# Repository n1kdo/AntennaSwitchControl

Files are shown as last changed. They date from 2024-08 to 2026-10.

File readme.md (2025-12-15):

# N1KDO IOT Antenna Switch Control

This project is intended to operate a remote antenna switch.  

It supports (up to) a 2-radio, 8-antenna switch.  2x6 switches for fine.  Active-hi
or active low compatible.

Why IOT?  That's really about WiFi.  The board uses WiFi to connect to your network,
which means that only the power leads need to be protected from Zeus, not 14 +/- wires.  

I have built matching "band-decoders" to interface with my Elecraft HF radios.  
The band decoders detect a band change on the radio and send a API request to 
the switch control board to request an antenna for that band.  If no antenna 
is available, the band decoder will activate the K3s' "TX INHIBIT" lead and 
prevent the radio from transmitting into the wrong antenna or no antenna.

The Band Selector (radio interface) is [here](https://github.com/n1kdo/BandSelector) &mdash;
This is the other component for this project, you will need _two_ &mdash;  one for each radio.

See the Ecosystem diagram, below.

## Ecosystem

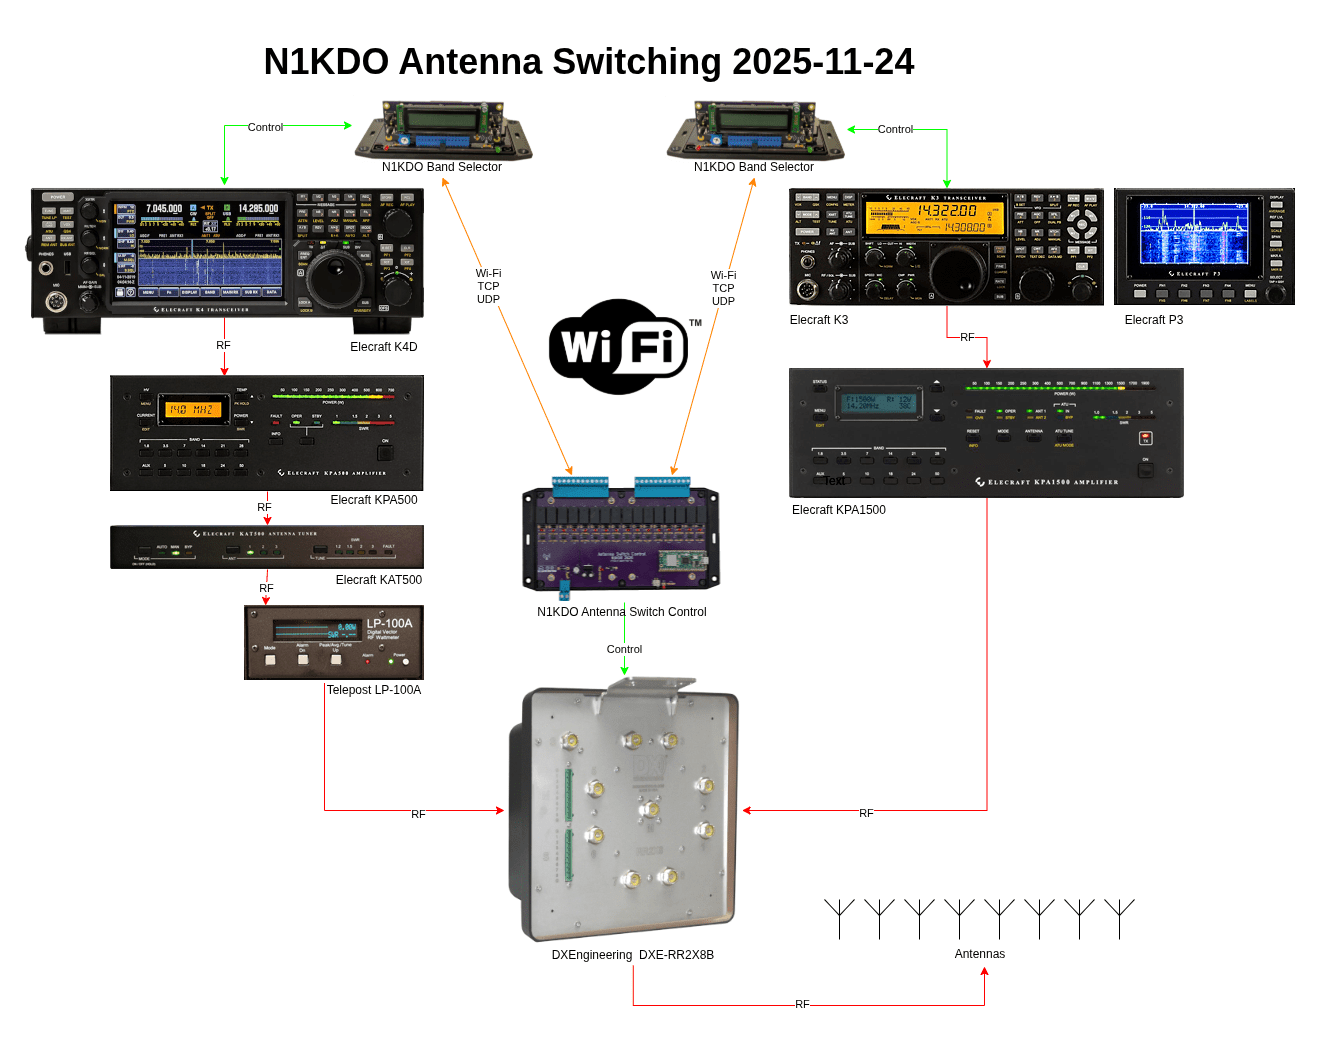
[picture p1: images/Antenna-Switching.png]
Ecosystem


## Bill of Materials

* [Bill of Materials](BOM.md)
* The approximate cost to buy these parts is about $106.

## Board Image

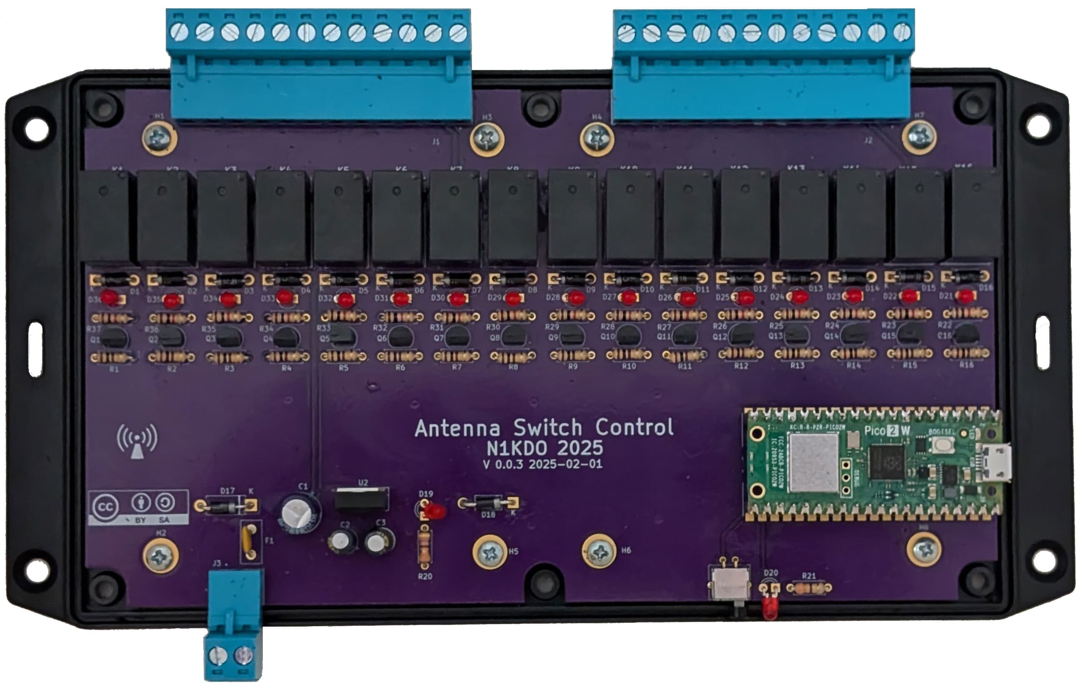
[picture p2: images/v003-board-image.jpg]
Board Image


# UI Images

## "Control Panel" Image

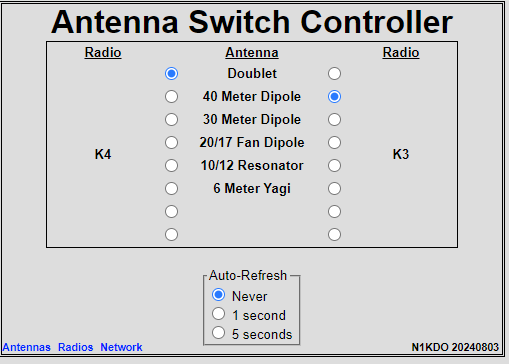
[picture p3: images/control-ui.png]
Control UI


## Antenna Setup UI

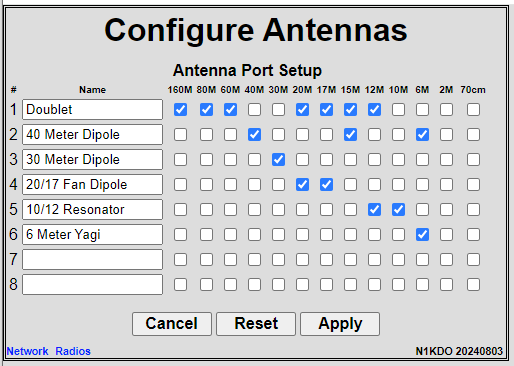
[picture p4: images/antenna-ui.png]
Antenna Setup UI


## Radio Setup UI

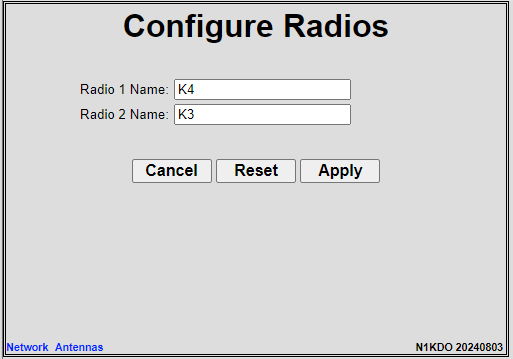
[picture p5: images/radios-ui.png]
Radio Setup UI


## Network Setup UI

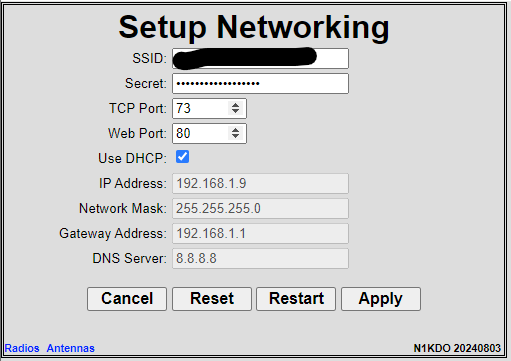
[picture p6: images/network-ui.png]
Network Setup UI


n1kdo 20251124

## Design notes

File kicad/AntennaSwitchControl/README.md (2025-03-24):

# Antenna Switch Control (Hardware)

This is a board that allows a Raspberry Pi Pico-W to control 16 SPST relays.

The original purpose is to provide better automation for a 2-in, 6-out remote antenna switch, but
it is built with extra capacity to allow a 2-in, 8-out remote switch as well.

## 3D image from KiCad
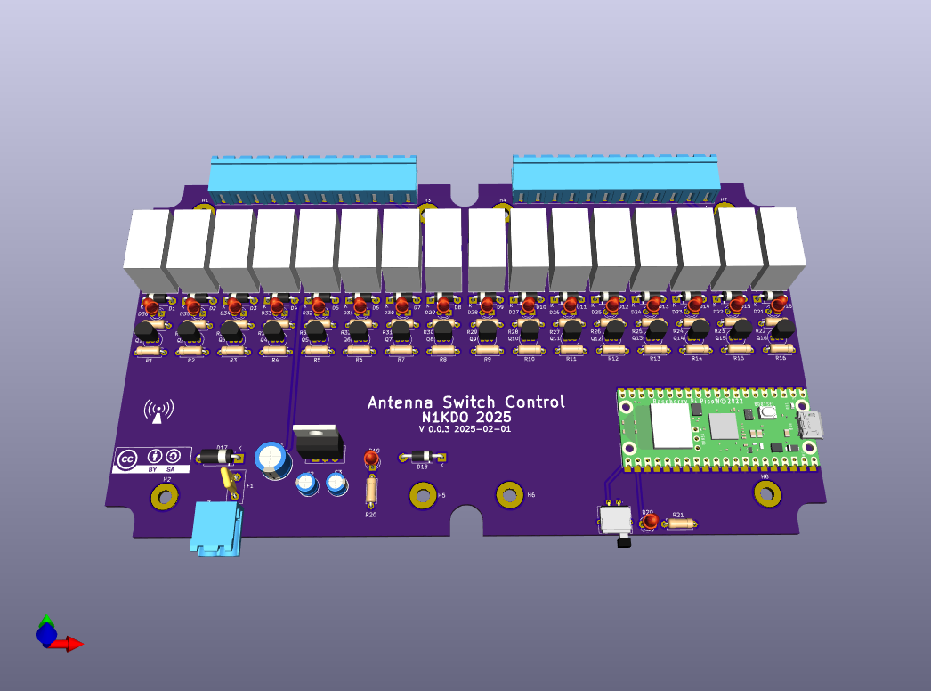
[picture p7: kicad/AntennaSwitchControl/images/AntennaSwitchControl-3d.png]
3d image


## Real World Image

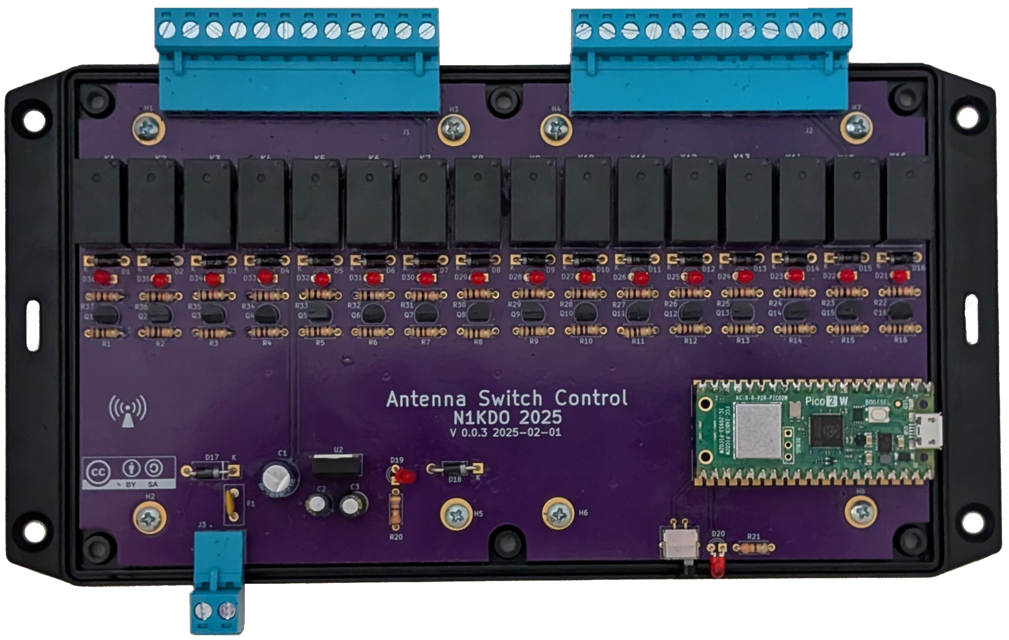
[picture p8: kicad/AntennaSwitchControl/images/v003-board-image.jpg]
Real-World Image


20250324 n1kdo

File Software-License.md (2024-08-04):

# BSD 2-Clause License

**Copyright (c) 2024, Jeffrey B. Otterson, N1KDO**

All rights reserved.

Redistribution and use in source and binary forms, with or without
modification, are permitted provided that the following conditions are met:

* Redistributions of source code must retain the above copyright notice, this
  list of conditions and the following disclaimer.

* Redistributions in binary form must reproduce the above copyright notice,
  this list of conditions and the following disclaimer in the documentation
  and/or other materials provided with the distribution.

**THIS SOFTWARE IS PROVIDED BY THE COPYRIGHT HOLDERS AND CONTRIBUTORS "AS IS"
AND ANY EXPRESS OR IMPLIED WARRANTIES, INCLUDING, BUT NOT LIMITED TO, THE
IMPLIED WARRANTIES OF MERCHANTABILITY AND FITNESS FOR A PARTICULAR PURPOSE ARE
DISCLAIMED. IN NO EVENT SHALL THE COPYRIGHT HOLDER OR CONTRIBUTORS BE LIABLE
FOR ANY DIRECT, INDIRECT, INCIDENTAL, SPECIAL, EXEMPLARY, OR CONSEQUENTIAL
DAMAGES (INCLUDING, BUT NOT LIMITED TO, PROCUREMENT OF SUBSTITUTE GOODS OR
SERVICES; LOSS OF USE, DATA, OR PROFITS; OR BUSINESS INTERRUPTION) HOWEVER
CAUSED AND ON ANY THEORY OF LIABILITY, WHETHER IN CONTRACT, STRICT LIABILITY,
OR TORT (INCLUDING NEGLIGENCE OR OTHERWISE) ARISING IN ANY WAY OUT OF THE USE
OF THIS SOFTWARE, EVEN IF ADVISED OF THE POSSIBILITY OF SUCH DAMAGE.**

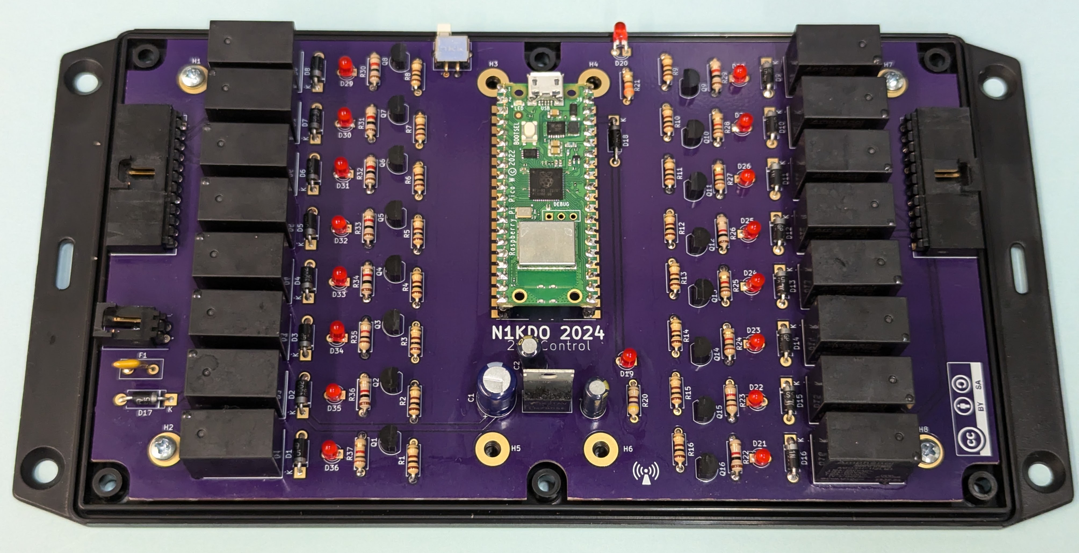
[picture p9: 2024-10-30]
kicad/AntennaSwitchControl/images/16-relays-reality.jpg

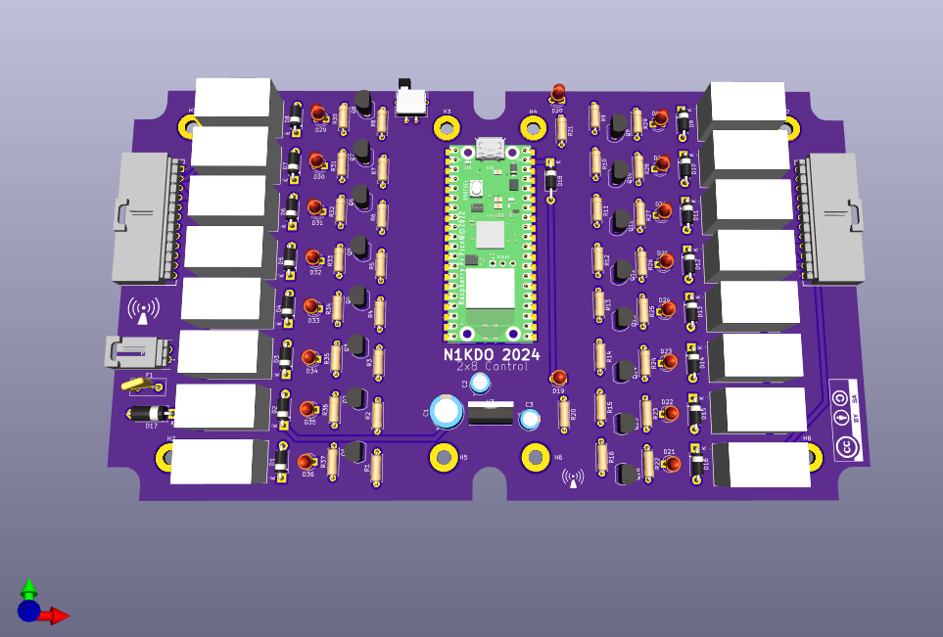
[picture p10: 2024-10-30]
kicad/AntennaSwitchControl/images/3d-render.png

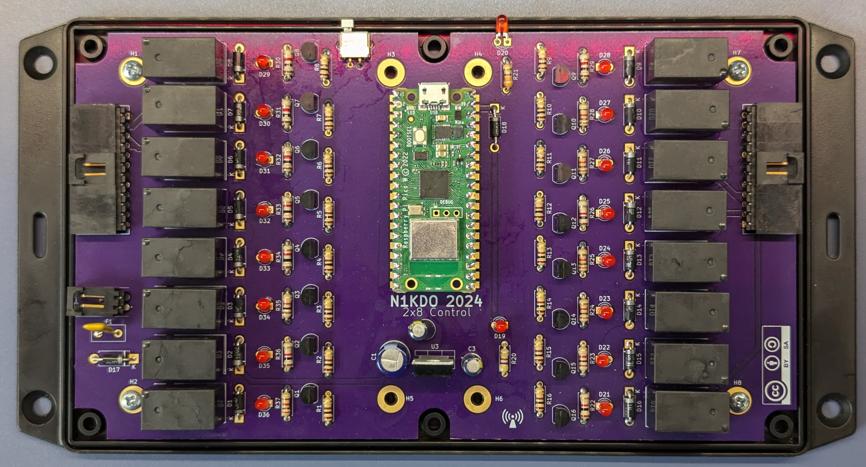
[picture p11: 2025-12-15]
images/board-image.jpg

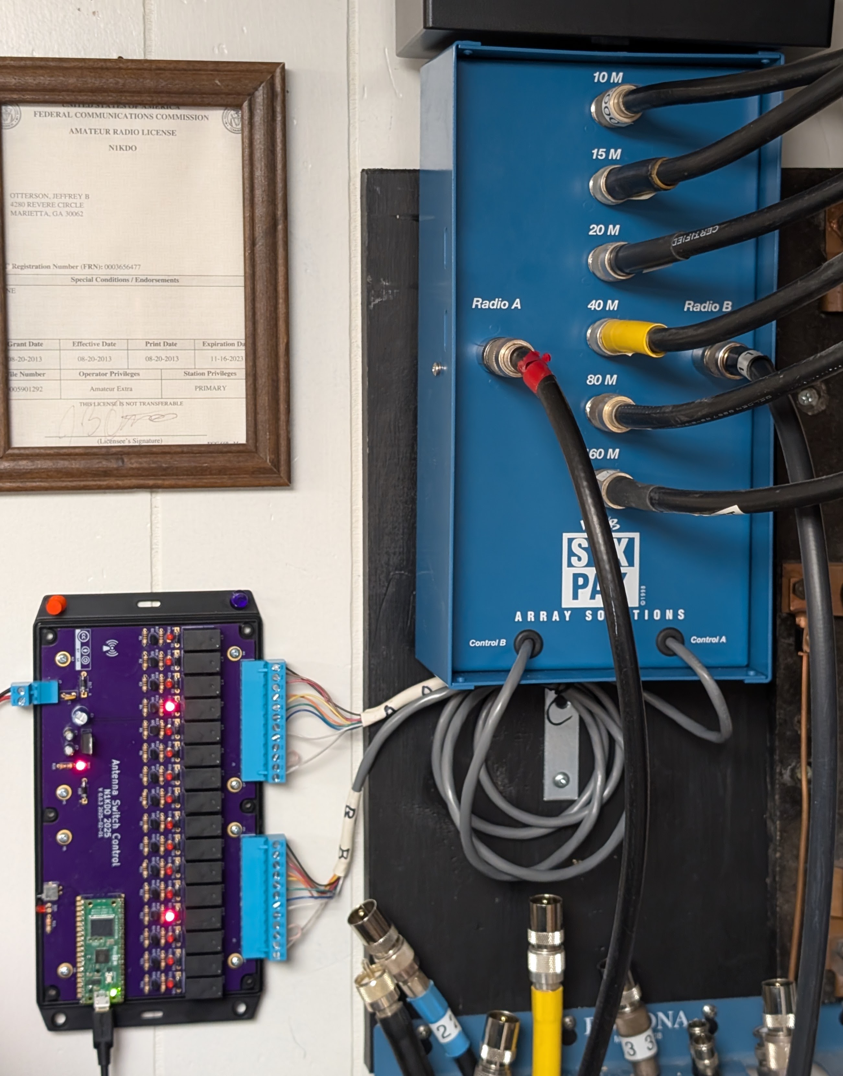
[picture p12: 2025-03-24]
images/with-six-pak.jpg

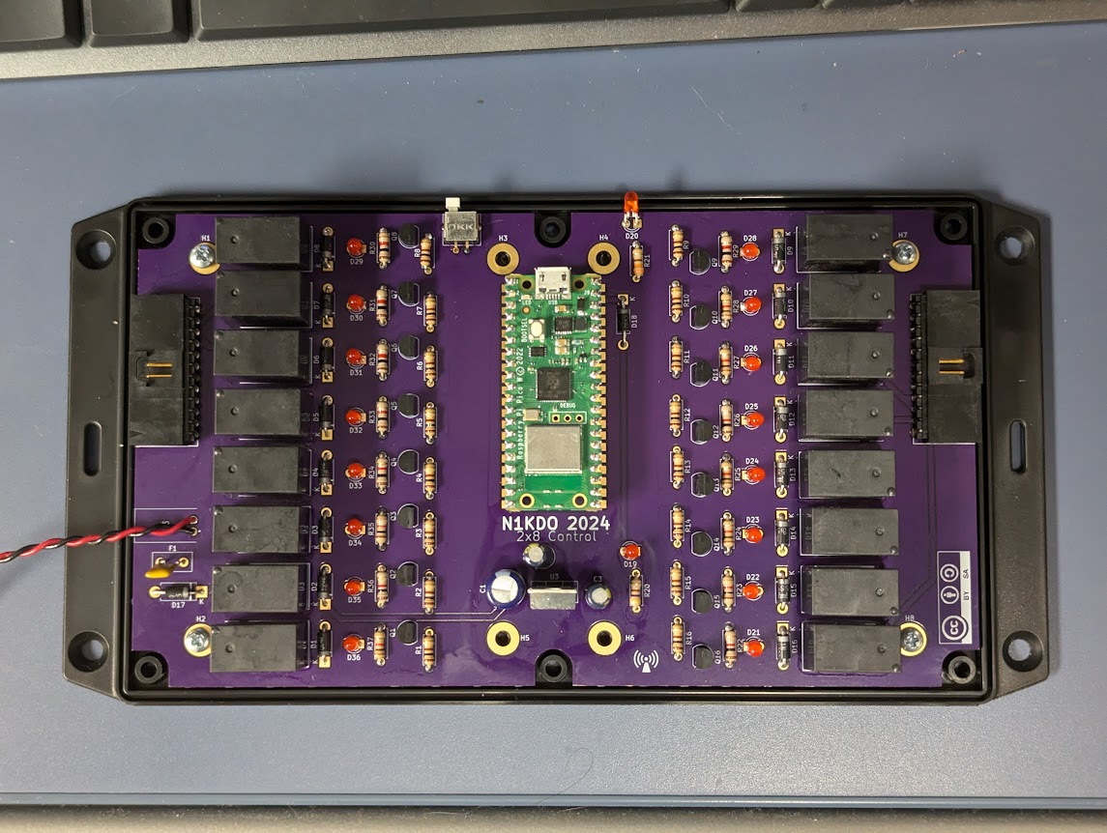
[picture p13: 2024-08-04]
images/board-image.png

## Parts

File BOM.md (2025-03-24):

# Bill of Materials for Antenna Switch Controller

This is the Bill of Materials for the N1KDO Antenna Switch Controller.

All the parts -- except the circuit boards -- were ordered from Mouser.com.

The circuit boards came from Oshpark.com.

## Antenna Switch Controller Board Bill of Materials

| ID | Description | Manufacturer | Part Number | Qty | Price | Extended |
|---|---|---|---|----:|---:|---:|
| C1 | Aluminum Electrolytic Capacitors - Radial Leaded 220uF 25V | Panasonic | ECA-1EM221 | 1 |  0.28 | 0.28 |
| C2,C3 | Aluminum Electrolytic Capacitors - Radial Leaded 2.2uF 50volts AEC-Q200 | Panasonic | EEU-FC1H2R2H | 2 |  0.12 | 0.24 |
| D1,D2,D3,D4,D5,D6,D7,D8,D9,D10,<br/>D11,D12,D13,D14,D15,D16,D17 | Rectifiers Diode - DO-41 - 100V - 1A | Diotec | 1N4002 |  17 |  0.06 | 1.02 |
| D18 | Schottky Diodes & Rectifiers Vr/40V Io/1A | STMicroelectronics | 1N5819 | 1 |  0.21 | 0.21 |
| D19,D20,D21,D22,D23,D24,D25,D26,D27,<br/>D28,D29,D30,D31,D32,D33,D34,D35,D36 | Standard LEDs - Through Hole Red Diffused | Lite-On | LTL-4221N |  18 |  0.19 | 3.42 |
| F1 | Resettable Fuses - PPTC .9A 30V 100A Imax | LittelFuse | RUEF090 | 1 |  0.61 | 0.61 |
| J1,J2 | Pluggable Terminal Blocks 2 24 Poles, Pluggable, Receptacle, Horizontal, 5.0 Pitch, Terminal Block  | SameSky | TBP04R1-500-12BE | 2 |  1.12 | 2.24 | 
| J3 | Pluggable Terminal Blocks 2 24 Poles, Pluggable, Receptacle, Horizontal, 5.0 Pitch, Terminal Block  | SameSky | TBP04R1-500-02BE | 1 |  0.43 | 0.43 |
| K1,K2,K3,K4,K5,K6,K7,K8,<br/>K9,K10,K11,K12,K13,K14,K15,K16 | General Purpose Relays Commercial Relay Rated Carrying Current 10A | Amphenol Anytek | AHQSH112LM100G |  16 |  0.53 | 8.48 |
| Q1,Q2,Q3,Q4,Q5,Q6,Q7,Q8,<br/>Q9,Q10,Q11,Q12,Q13,Q14,Q15,Q16 | MOSFET 60V 200mA 5 Ohm Single N-Channel TO-92 | onsemi / Fairchild | 2N7000 |  16 |  0.38 | 6.08 |
| R1,R2,R3,R4,R5,R6,R7,R8<br/>R9,R10,R11,R12,R13,R14,R15,R16 | Carbon Film Resistors - Through Hole 1/4W 100 Ohm 5% | Yageo | CFR-25JB-52-100R |  15 |  0.04 | 0.60 |
| R20 | Carbon Film Resistors - Through Hole 1/4W 470 Ohm 5% | Yageo | CFR-25JB-52-470R | 1 |  0.02 | 0.02 |
| R21 | Carbon Film Resistors - Through Hole 1/4W 330 Ohm 5% | Yageo | CFR-25JB-52-330R | 1 |  0.02 | 0.02 |
| R22,R23,R24,R25,R26,R27,R28,R29,<br/>R30,R31,R32,R33,R34,R35,R36,R37 | Carbon Film Resistors - Through Hole 1 kOhms 250 mW 5 % | Yageo | CFR-25JB-1K0 |  16 |  0.02 | 0.32 |
| SW1 | Pushbutton Switches SPST OFF(ON) R/A WHT | NKK Switches | GB215AH-B | 1 |  4.35 | 4.35 |
| SW1 (cap) | Switch Bezels / Switch Caps .157" RND BLK CAP | NKK Switches | AT4063A | 1 |  0.52 | 0.52 |
| U1 | Single Board Computers Raspberry Pi Pico 2 W | Raspberry Pi | SC1633 | 1 |  7.00 | 7.00 |
| U3 | Linear Voltage Regulators 5.0V 1.5A Positive | STMicroelectronics | L7805CV | 1 |  0.48 | 0.48 |
| Enclosure | Enclosures, Boxes, & Cases FR ABS w/Flanged Lid 7.6x4.4x2.2" Black | Hammond Manufacturing | 1591XXEFLBK | 1 | 12.84 | 12.84 |
| P1, P2 | Pluggable Terminal Blocks 2 24 Poles, Pluggable, Horizontal, 5.0 Pitch, 28 12 (AWG), Terminal Block | SameSky | TBP04P1-500-12BE | 2 |  2.52 | 5.04 |
| P3 | Pluggable Terminal Blocks 2 24 Poles, Pluggable, Horizontal, 5.0 Pitch, 28 12 (AWG), Terminal Block | SameSky | TBP04R1-500-02BE | 1 |  0.83 | 0.83 |
| PCB | N1KDO Antenna Switch Control PCB Band Selector Board PCB V 0.0.3 | Oshpark | | 1 | 50.08 | 50.08 |
| **Total** | | | | | | **105.11** |

Approximate Total Project Cost $106.

n1kdo 20250324

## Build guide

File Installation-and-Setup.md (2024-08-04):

# Installation and Setup

This page describes how to install and set up this project.

There are three main steps:

1. Installing Micropython
2. Installing the Python code.
3. Connecting to your Wi-Fi network.

## Installing MicroPython on your Pico-W

1. Download the latest stable build of [Pico W MicroPython](https://micropython.org/download/RPI_PICO_W/). 
   [This is the direct link](https://micropython.org/resources/firmware/RPI_PICO_W-20240105-v1.22.1.uf2).
2. Connect a micro-USB cable to your PC.  Hold down the white "BOOTSEL" button on the Pico-W, and insert the
   micro-USB cable into your Pico-W.
3. The Pico-W should appear as a USB storage device on your computer.  On mine, it shows up as "RPI-RP2 (F:)".
4. Copy/Paste the MicroPython .uf2 file to this drive.
5. Disconnect the Pico-W and prepare for the next step.

## Installing this software onto the Pico-W

The easiest way to get this software installed onto your Pico-W is to use the `loader.py` tool, also
provided in this repository.  

Note that these commands are written from a Windows perspective, but the Python commands should work the same way 
on macOS or Linux.  I have no Macs, so I cannot test this.

1. Download Python 3 from https://www.python.org/downloads/ and install it.  Make sure to select "Add 
   Python 3 to Path."
2. Download the contents of this GitHub repository as a zip.  Use
   [this URL](https://github.com/n1kdo/switch-control/archive/refs/heads/master.zip)
3. Unpack that zip file somewhere. 
4. Open a command prompt.  (your choice.  Could be PowerShell, could be good old CMD.)
5. From the command line, execute the following command: `pip install pyserial` -- this will install the Python 
   serial port support.
6. Change directory to where you unpacked the GitHub zip file, and then change directory to the `src/loader` directory.
7. From the command line, execute the following command: `python loader.py` -- this will install all the python  
   software onto the Pico-W.

If you want to experiment, you can use the open-source "Thonny" IDE to load the python source code and HTML files
onto the Pico W.  Unfortunately, Thonny cannot load binary files, but you can work around this "upload" feature in
the "Files" page.

## Setup and Connecting to your Wi-Fi Network

The software has a setup web page that allows you to set the SSID and secret to connect to you Wi-Fi network, 
but how can you access this page if the controller is not already connected to your network? This is the function
of the "mode" button. When the mode button is pressed, the device will restart as a Wi-Fi access point named
"kpa500" using password "elecraft".  Connect to this access point with your phone or other Wi-Fi device. Some 
devices will complain that this network does not offer Internet access--that is ok, because it does not! 
You may need to check a box to keep your device connected to this network.

Once connected to the "kpa500" network, open the device's web page by accessing http://192.168.4.1 – from here you
can click the "Setup" link and configure the network. After you enter your network’s SSID and secret, click the "Apply"
button to save the configuration, and then press the "Restart" button to return the device to normal mode.

Access point mode can also be used in locations where there is no Wi-Fi service, the device is completely 
usable in access point mode.

## Electrical Connections

(To be added.  Meanwhile, consult the schematic.)

## Controls and Indicators

| Control/Indicator | Purpose |
|---|---|
| LED D20 | Status indicator |
| Switch SW1 | Mode Selector |

The Status Indicator normally blinks out the device's IP address in slow Morse code.  
When the device is configured in Access Point mode, it will blink out "AP" followed by the device's IP address. 
If the device cannot connect to the Wi-Fi network, it will blink "ERR" in Morse code.

Hold down the Mode Selector button two seconds to switch the device in or out of Access Point Mode (for configuring
the Wi-Fi network.) The device will restart, and you should see a different message blinking out in Morse code.

## What is all this software stuff, anyway?

Here's a brief guide to what all code is...

### Application files:

This table describes what the source modules do.

| Filename | Description |
|---|---|
| src/switch-control/http_server.py | this is a lightweight HTTP ("web") server. |
| src/switch-control/main.py | mainline program. |
| src/switch-control/micro_logging.py | lightweight logging, similar to Python's 'logging' |
| src/switch-control/morse_code.py | code to send morse code on the LED.  Not all letters are included to save space. |
| src/switch-control/not_machine.py | mock 'machine' interface, for debugging on platforms other than MicroPython. |
| src/switch-control/picow_network.py | networking common code for Pico-W |
| src/switch-control/relays.py | relay control code |
| src/switch-control/utils.py | common utility functions |
| src/switch-control/content/antennas.html | Antennas Configuration page |
| src/switch-control/content/favicon.ico | Icon for web site |
| src/switch-control/content/files.html | Files page |
| src/switch-control/content/network.html  | Network Configuration Page |
| src/switch-control/content/radios.html | Radios Configuration Page |
| src/switch-control/content/switch.html | Switch Control Panel Page |
| src/switch-control/data/config.json | configuration file for device. |

Note that it is possible to modify any of the User Interface pages.  The software wants to protect these files, you
will need to upload them using a different name, and then rename them.

If you feel adventurous, you can modify the `config.json` file to set your Wi-Fi SSID and secret prior to loading the
software.

### Additional Stuff

Here's the code that makes up the "Easy Loader".

| Filename | Description |
|---|---|
| src/loader/loader.py  | tool to more easily install Python code on Pico W |
| src/loader/pyboard.py | code to allow communication and control of MicroPython boards, used by loader.py. |

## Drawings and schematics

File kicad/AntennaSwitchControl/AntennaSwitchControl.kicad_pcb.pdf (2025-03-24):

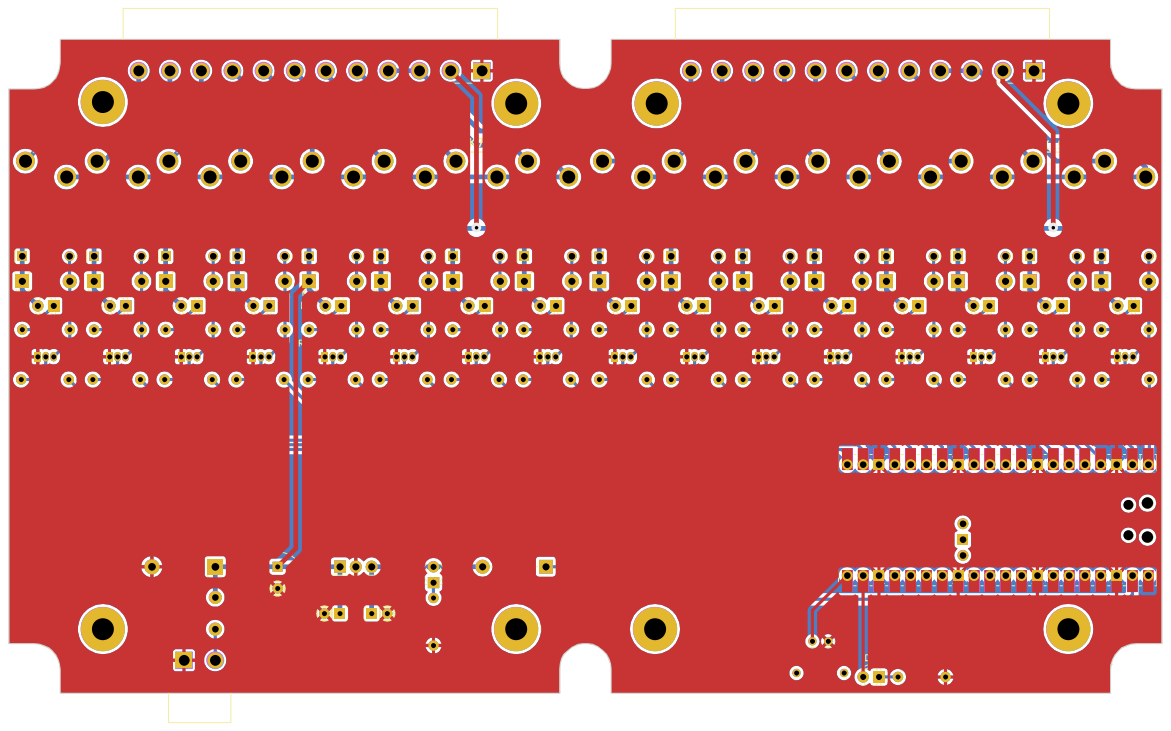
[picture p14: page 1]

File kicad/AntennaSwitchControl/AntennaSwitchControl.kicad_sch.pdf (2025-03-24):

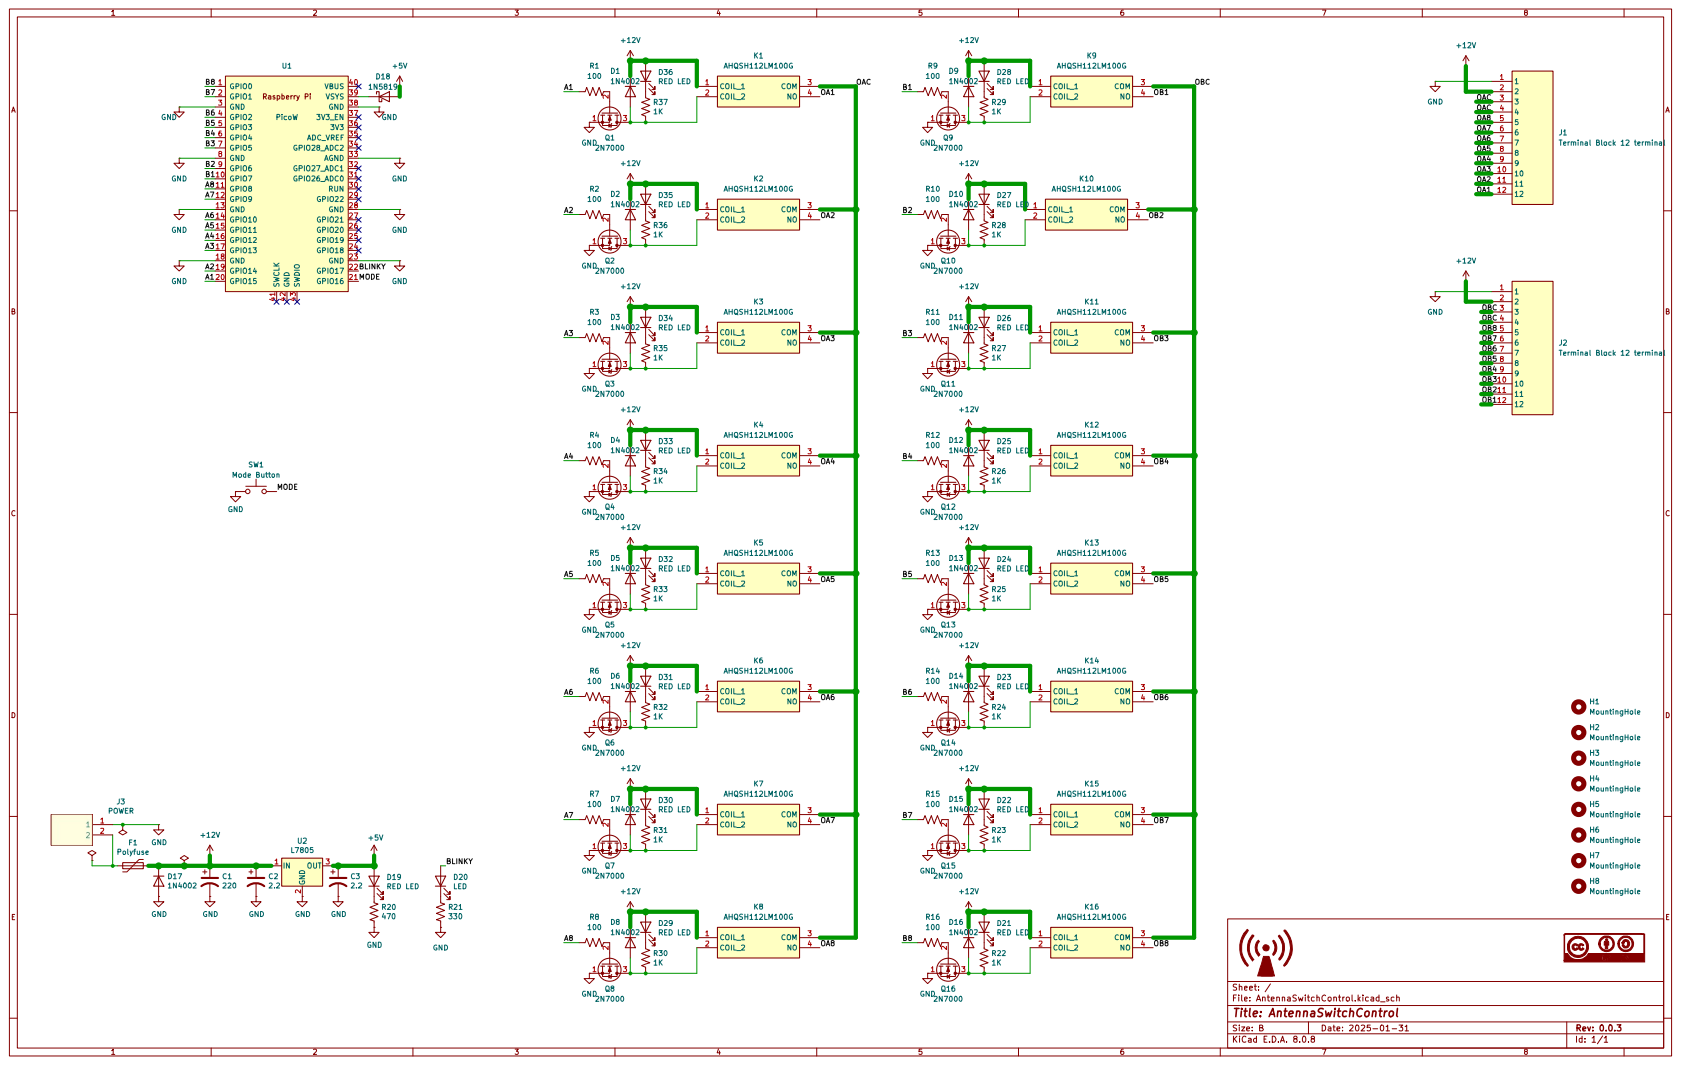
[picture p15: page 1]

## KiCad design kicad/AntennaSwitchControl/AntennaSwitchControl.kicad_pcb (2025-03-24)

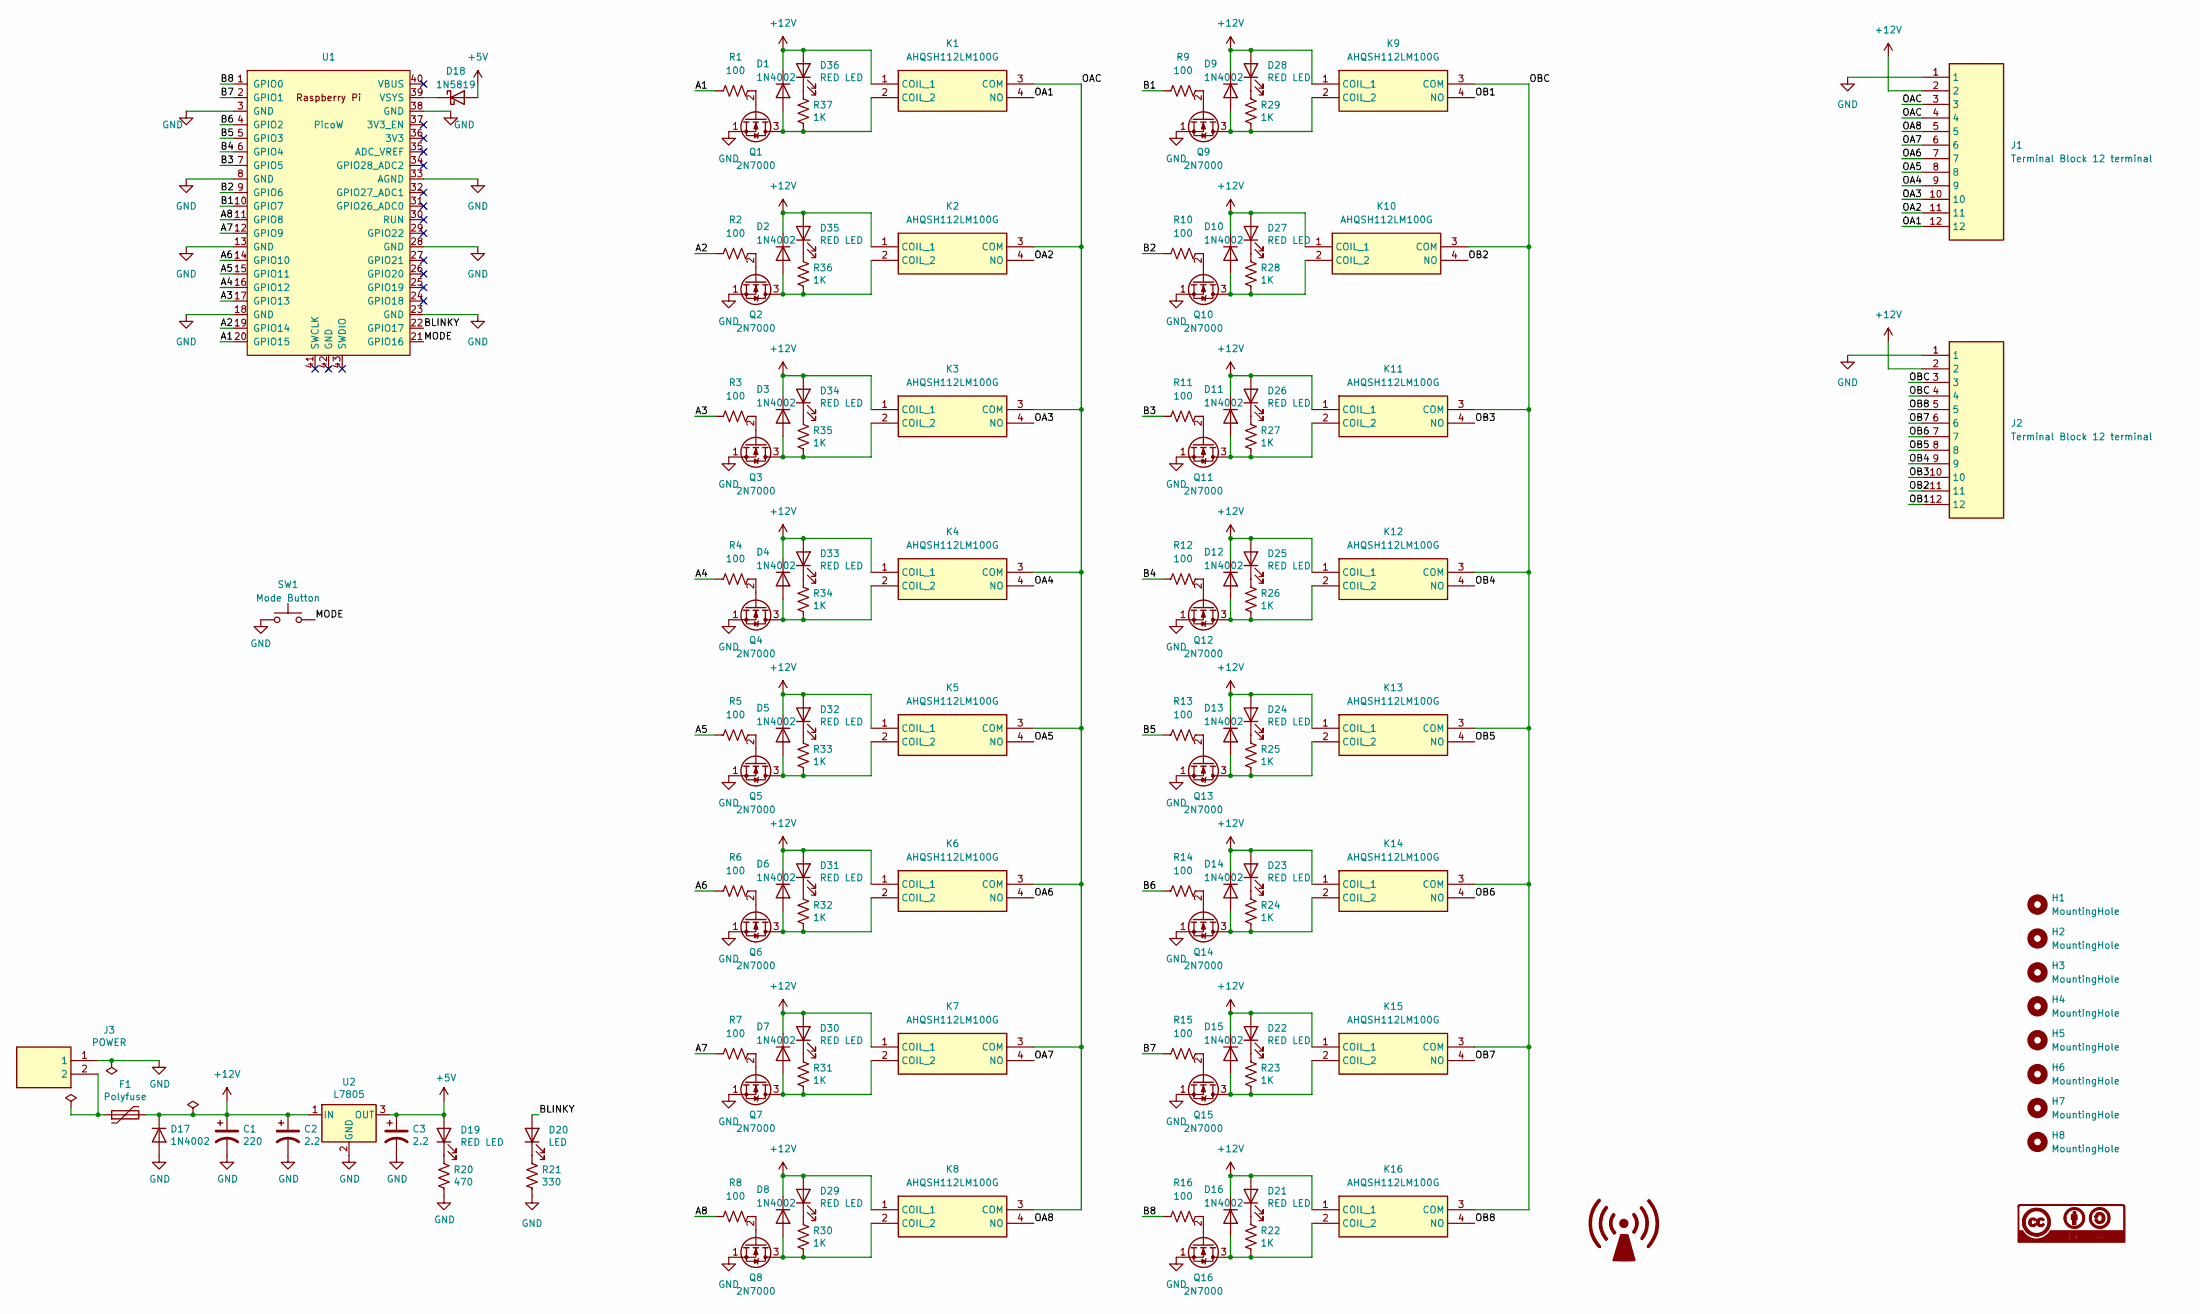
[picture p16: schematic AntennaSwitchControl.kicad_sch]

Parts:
C1: 220; CP_Radial_D8.0mm_P3.50mm; Part ECA-1EM221
C2, C3: 2.2; CP_Radial_D5.0mm_P2.50mm; Part EEU-FC1H2R2H
D1, D2, D3, D4, D5, D6, D7, D8, D9, D10, D11, D12, D13, D14, D15, D16: 1N4002; D_DO-41_SOD81_P7.62mm_Horizontal
D17: 1N4002; D_DO-15_P10.16mm_Horizontal; Part 1n4002
D18: 1N5819; D_DO-41_SOD81_P10.16mm_Horizontal
D19: RED LED; LED_D3.0mm
D20: LED; LED_D3.0mm
D21, D22, D23, D24, D25, D26, D27, D28, D29, D30, D31, D32, D33, D34, D35, D36: RED LED; LED_D3.0mm; Part AP2012HD
F1: Polyfuse; RUEF090; Part 30R090UU
H1, H2, H3, H4, H5, H6, H7, H8: MountingHole; MountingHole_3.5mm_Pad
J1, J2: Terminal Block 12 terminal; CUI_TBP04R1-500-12BE; Mouser Part Number 179-TBP04R1-500-12BE
J3: POWER; CUI_TBP04R1-500-02BE; Part TBP04R1-500-02BE; Mouser Part Number 179-TBP04R1-500-02BE
K1, K2, K3, K4, K5, K6, K7, K8, K9, K10, K11, K12, K13, K14, K15, K16: AHQSH112LM100G; AHQSH112LM112G; Mouser Part Number 523-AHQSH105LM100G
Q1, Q2, Q3, Q4, Q5, Q6, Q7, Q8, Q9, Q10, Q11, Q12, Q13, Q14, Q15, Q16: 2N7000; TO-92_Inline
R1, R2, R3, R4, R5, R6, R7, R8, R9, R10, R11, R12, R13, R14, R15, R16: 100; R_Axial_DIN0207_L6.3mm_D2.5mm_P7.62mm_Horizontal
R20: 470; R_Axial_DIN0207_L6.3mm_D2.5mm_P7.62mm_Horizontal; Part ERJ-6GEYJ471V
R21: 330; R_Axial_DIN0207_L6.3mm_D2.5mm_P7.62mm_Horizontal; Part ERJ-6GEYJ471V
R22, R23, R24, R25, R26, R27, R28, R29, R30, R31, R32, R33, R34, R35, R36, R37: 1K; R_Axial_DIN0207_L6.3mm_D2.5mm_P7.62mm_Horizontal; Part ERJ-6GEYJ471V
SW1: Mode Button; GB215AHB; part GB215AH
U1: PicoW; RPi_PicoW_SMD_TH
U2: L7805; TO-220-3_Vertical; Part L7805CDT-TR

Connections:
+5V: C3.1, D18.2 (A), D19.2 (A), U2.3 (OUT)
+12V: C1.1, C2.1, D1.1 (K), D2.1 (K), D3.1 (K), D4.1 (K), D5.1 (K), D6.1 (K), D7.1 (K), D8.1 (K), D9.1 (K), D10.1 (K), D11.1 (K), D12.1 (K), D13.1 (K), D14.1 (K), D15.1 (K), D16.1 (K), D17.1 (K), D21.2 (A), D22.2 (A), D23.2 (A), D24.2 (A), D25.2 (A), D26.2 (A), D27.2 (A), D28.2 (A), D29.2 (A), D30.2 (A), D31.2 (A), D32.2 (A), D33.2 (A), D34.2 (A), D35.2 (A), D36.2 (A), F1.2, J1.2, J2.2, K1.1 (COIL_1), K2.1 (COIL_1), K3.1 (COIL_1), K4.1 (COIL_1), K5.1 (COIL_1), K6.1 (COIL_1), K7.1 (COIL_1), K8.1 (COIL_1), K9.1 (COIL_1), K10.1 (COIL_1), K11.1 (COIL_1), K12.1 (COIL_1), K13.1 (COIL_1), K14.1 (COIL_1), K15.1 (COIL_1), K16.1 (COIL_1), U2.1 (IN)
/A1: R1.1, U1.20 (GPIO15)
/A2: R2.1, U1.19 (GPIO14)
/A3: R3.1, U1.17 (GPIO13)
/A4: R4.1, U1.16 (GPIO12)
/A5: R5.1, U1.15 (GPIO11)
/A6: R6.1, U1.14 (GPIO10)
/A7: R7.1, U1.12 (GPIO9)
/A8: R8.1, U1.11 (GPIO8)
/B1: R9.1, U1.10 (GPIO7)
/B2: R10.1, U1.9 (GPIO6)
/B3: R11.1, U1.7 (GPIO5)
/B4: R12.1, U1.6 (GPIO4)
/B5: R13.1, U1.5 (GPIO3)
/B6: R14.1, U1.4 (GPIO2)
/B7: R15.1, U1.2 (GPIO1)
/B8: R16.1, U1.1 (GPIO0)
/BLINKY: D20.2 (A), U1.22 (GPIO17)
/MODE: SW1.2, U1.21 (GPIO16)
/OA1: J1.12, K1.4 (NO)
/OA2: J1.11, K2.4 (NO)
/OA3: J1.10, K3.4 (NO)
/OA4: J1.9, K4.4 (NO)
/OA5: J1.8, K5.4 (NO)
/OA6: J1.7, K6.4 (NO)
/OA7: J1.6, K7.4 (NO)
/OA8: J1.5, K8.4 (NO)
/OAC: J1.3, J1.4, K1.3 (COM), K2.3 (COM), K3.3 (COM), K4.3 (COM), K5.3 (COM), K6.3 (COM), K7.3 (COM), K8.3 (COM)
/OB1: J2.12, K9.4 (NO)
/OB2: J2.11, K10.4 (NO)
/OB3: J2.10, K11.4 (NO)
/OB4: J2.9, K12.4 (NO)
/OB5: J2.8, K13.4 (NO)
/OB6: J2.7, K14.4 (NO)
/OB7: J2.6, K15.4 (NO)
/OB8: J2.5, K16.4 (NO)
/OBC: J2.3, J2.4, K9.3 (COM), K10.3 (COM), K11.3 (COM), K12.3 (COM), K13.3 (COM), K14.3 (COM), K15.3 (COM), K16.3 (COM)
GND: C1.2, C2.2, C3.2, D17.2 (A), J1.1, J2.1, J3.1, Q1.1 (S), Q2.1 (S), Q3.1 (S), Q4.1 (S), Q5.1 (S), Q6.1 (S), Q7.1 (S), Q8.1 (S), Q9.1 (S), Q10.1 (S), Q11.1 (S), Q12.1 (S), Q13.1 (S), Q14.1 (S), Q15.1 (S), Q16.1 (S), R20.2, R21.2, SW1.1, U1.3 (GND), U1.8 (GND), U1.13 (GND), U1.18 (GND), U1.23 (GND), U1.28 (GND), U1.33 (AGND), U1.38 (GND), U2.2 (GND)
unnamed: D1.2 (A), K1.2 (COIL_2), Q1.3 (D), R37.2
unnamed: D2.2 (A), K2.2 (COIL_2), Q2.3 (D), R36.2
unnamed: D3.2 (A), K3.2 (COIL_2), Q3.3 (D), R35.2
unnamed: D4.2 (A), K4.2 (COIL_2), Q4.3 (D), R34.2
unnamed: D5.2 (A), K5.2 (COIL_2), Q5.3 (D), R33.2
unnamed: D6.2 (A), K6.2 (COIL_2), Q6.3 (D), R32.2
unnamed: D7.2 (A), K7.2 (COIL_2), Q7.3 (D), R31.2
unnamed: D8.2 (A), K8.2 (COIL_2), Q8.3 (D), R30.2
unnamed: D9.2 (A), K9.2 (COIL_2), Q9.3 (D), R29.2
unnamed: D10.2 (A), K10.2 (COIL_2), Q10.3 (D), R28.2
unnamed: D11.2 (A), K11.2 (COIL_2), Q11.3 (D), R27.2
unnamed: D12.2 (A), K12.2 (COIL_2), Q12.3 (D), R26.2
unnamed: D13.2 (A), K13.2 (COIL_2), Q13.3 (D), R25.2
unnamed: D14.2 (A), K14.2 (COIL_2), Q14.3 (D), R24.2
unnamed: D15.2 (A), K15.2 (COIL_2), Q15.3 (D), R23.2
unnamed: D16.2 (A), K16.2 (COIL_2), Q16.3 (D), R22.2
unnamed: D18.1 (K), U1.39 (VSYS)
unnamed: D19.1 (K), R20.1
unnamed: D20.1 (K), R21.1
unnamed: D21.1 (K), R22.1
unnamed: D22.1 (K), R23.1
unnamed: D23.1 (K), R24.1
unnamed: D24.1 (K), R25.1
unnamed: D25.1 (K), R26.1
unnamed: D26.1 (K), R27.1
unnamed: D27.1 (K), R28.1
unnamed: D28.1 (K), R29.1
unnamed: D29.1 (K), R30.1
unnamed: D30.1 (K), R31.1
unnamed: D31.1 (K), R32.1
unnamed: D32.1 (K), R33.1
unnamed: D33.1 (K), R34.1
unnamed: D34.1 (K), R35.1
unnamed: D35.1 (K), R36.1
unnamed: D36.1 (K), R37.1
unnamed: F1.1, J3.2
unnamed: Q1.2 (G), R1.2
unnamed: Q2.2 (G), R2.2
unnamed: Q3.2 (G), R3.2
unnamed: Q4.2 (G), R4.2
unnamed: Q5.2 (G), R5.2
unnamed: Q6.2 (G), R6.2
unnamed: Q7.2 (G), R7.2
unnamed: Q8.2 (G), R8.2
unnamed: Q9.2 (G), R9.2
unnamed: Q10.2 (G), R10.2
unnamed: Q11.2 (G), R11.2
unnamed: Q12.2 (G), R12.2
unnamed: Q13.2 (G), R13.2
unnamed: Q14.2 (G), R14.2
unnamed: Q15.2 (G), R15.2
unnamed: Q16.2 (G), R16.2

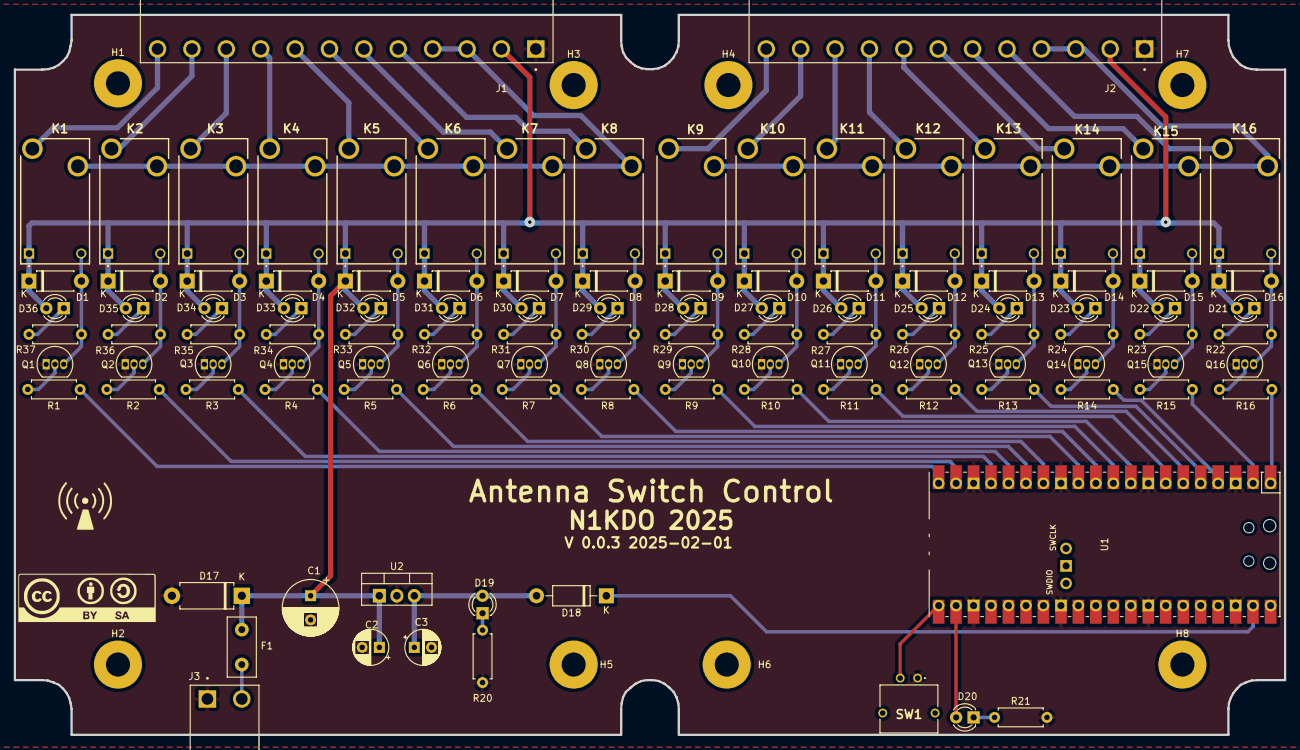
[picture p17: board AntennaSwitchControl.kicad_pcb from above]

Board: 2 copper layers, 184.7 x 104.7 mm, 122 parts (0 on the bottom side), 91 nets.

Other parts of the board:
G1: LOGO; non-ionizing-bigger
Ref**: Val**; CC-BY-SA

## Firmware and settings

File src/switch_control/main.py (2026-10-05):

#
# main.py -- this is the web server for the Raspberry Pi Pico W 6/8x2 switch controller.
#

__author__ = 'J. B. Otterson'
__copyright__ = 'Copyright 2022, 2026 J. B. Otterson N1KDO.'
__version__ = '0.1.32'  # 2026-10-04

#
# Copyright 2022, 2026 J. B. Otterson N1KDO.
#
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
import json
import socket
import time

from http_server import (HttpServer,
                         HTTP_STATUS_OK,
                         HTTP_STATUS_MOVED_PERMANENTLY,
                         HTTP_STATUS_BAD_REQUEST,
                         HTTP_STATUS_CONFLICT,
                         HTTP_VERB_GET, HTTP_VERB_POST)
from antennas_selected_data import AntennasSelectedData
from config_data import ConfigData
from morse_code import MorseCode
from ntp import get_ntp_time
from utils import is_hostname, is_ipv4, milliseconds, safe_int, upython
from relays import set_port
import micro_logging as logging
import udp_messages

import asyncio
if upython:
    from asyncio import TimeoutError  # micropython has no builtin TimeoutError
else:
    from asyncio.exceptions import TimeoutError  # same class as the builtin on 3.11+
if upython:
    import machine
    from picow_network import PicowNetwork
    try:
        from watchdog import Watchdog
    except ImportError:
        Watchdog = None
else:
    from not_machine import machine
    Watchdog = None
    def const(i):
        return i

BANDS = (b'None', b'160M', b'80M', b'60M', b'40M', b'30M', b'20M',
         b'17M', b'15M', b'12M', b'10M', b'6M', b'2M', b'70cm')
# antenna_bands is a BITMASK, 16 bits wide.
# noinspection PyUnboundLocalVariable
"""
BAND_160M_MASK = const(0x0001)
BAND_80M_MASK = const(0x0002)
BAND_60M_MASK = const(0x0004)
BAND_40M_MASK = const(0x0008)
BAND_30M_MASK = const(0x0010)
BAND_20M_MASK = const(0x0020)
BAND_17M_MASK = const(0x0040)
BAND_15M_MASK = const(0x0080)
BAND_12M_MASK = const(0x0100)
BAND_10M_MASK = const(0x0200)
BAND_6M_MASK = const(0x0400)
BAND_2M_MASK = const(0x0800)
BAND_70CM_MASK = const(0x1000)
BAND_OTHER1_MASK = const(0x2000)  # not used
BAND_OTHER2_MASK = const(0x4000)  # not used
BAND_OTHER3_MASK = const(0x8000)  # not used
"""

onboard = machine.Pin('LED', machine.Pin.OUT, value=1)  # turn on right away
morse_led = machine.Pin(17, machine.Pin.OUT, value=0)  # status/morse code LED on GPIO17 / pin 22
ap_mode_button = machine.Pin(16, machine.Pin.IN, machine.Pin.PULL_UP)  # mode button input on GPIO16 / pin 21

CONTENT_DIR = 'content/'

DEFAULT_SECRET = 'antenna-switch'
DEFAULT_SSID = 'switch'
DEFAULT_TCP_PORT = 73
DEFAULT_WEB_PORT = 80

# globals...
keep_running = True
_select_antenna_lock = asyncio.Lock()

# http server
http_server = HttpServer(content_dir=CONTENT_DIR)

# configuration data
antennas_selected = AntennasSelectedData()
config = ConfigData()


# noinspection PyUnusedLocal
@http_server.route(b'/')
async def slash_callback(http, verb, args, reader, writer, request_headers=None):  # callback for '/'
    # send redirect to /switch.html
    http_status = HTTP_STATUS_MOVED_PERMANENTLY
    bytes_sent = await http.send_simple_response(writer, http_status, None, None, [b'Location: /switch.html'])
    return bytes_sent, http_status


# noinspection PyUnusedLocal
@http_server.route(b'/api/config')
async def api_config_callback(http, verb, args, reader, writer, request_headers=None):  # callback for '/api/config'
    global config
    if verb == HTTP_VERB_GET:
        response = dict(config.get_data())  # copying config dict so removing secret does not trash original data
        response['secret'] = '' # do not return the secret
        http_status = HTTP_STATUS_OK
        bytes_sent = await http.send_simple_response(writer, http_status, http.CT_APP_JSON, response)
    elif verb == HTTP_VERB_POST:
        # A POST with no recognized configuration keys has nothing to do. That includes malformed JSON
        # bodies, which the server decodes as an empty dict -- do not pretend they succeeded.
        if not isinstance(args, dict) or not any(key in args for key in ('log_level', 'tcp_port',
                                                                         'web_port', 'SSID', 'secret',
                                                                         'hostname', 'dhcp',
                                                                         'ip_address', 'netmask',
                                                                         'gateway', 'dns_server',
                                                                         'antenna_bands', 'antenna_names',
                                                                         'radio_names')):
            response = b'no configuration data\r\n'
            http_status = HTTP_STATUS_BAD_REQUEST
            bytes_sent = await http.send_simple_response(writer, http_status, http.CT_TEXT_TEXT, response)
            return bytes_sent, http_status
        errors = False
        log_level = args.get('log_level')
        if log_level is not None:
            log_level = log_level.strip().upper()
            if log_level in ['DEBUG', 'INFO', 'WARNING', 'ERROR', 'CRITICAL']:
                config['log_level'] = log_level
            else:
                errors = True
                logging.warning(f'log level {log_level} not valid', 'main:api_config_callback')
        tcp_port = args.get('tcp_port')
        if tcp_port is not None:
            tcp_port_int = safe_int(tcp_port, -2)
            if 1 <= tcp_port_int <= 65535:
                config['tcp_port'] = tcp_port
            else:
                errors = True
                logging.warning(f'tcp_port {tcp_port_int} not valid', 'main:api_config_callback')
        web_port = args.get('web_port')
        if web_port is not None:
            web_port_int = safe_int(web_port, -2)
            if 1 <= web_port_int <= 65535:
                config['web_port'] = web_port
            else:
                errors = True
                logging.warning(f'web_port {web_port_int} not valid', 'main:api_config_callback')
        ssid = args.get('SSID')
        if ssid is not None:
            if 0 < len(ssid) <= 32:
                config['SSID'] = ssid
            else:
                errors = True
                logging.warning(f'ssid  {ssid} not valid', 'main:api_config_callback')
        secret = args.get('secret')
        if secret is not None and len(secret) > 0:
            if 8 <= len(secret) <= 64:
                config['secret'] = secret
            else:
                errors = True
                logging.warning(f'secret {secret} not valid', 'main:api_config_callback')
        hostname = args.get('hostname')
        if hostname is not None:
            if is_hostname(hostname):
                config['hostname'] = hostname
            else:
                errors = True
                logging.warning(f'hostname {hostname} not valid', 'main:api_config_callback')
        dhcp_arg = args.get('dhcp')
        if dhcp_arg is not None:
            config['dhcp'] = safe_int(dhcp_arg, 0) == 1
        ip_address = args.get('ip_address')
        if ip_address is not None:
            if ip_address == '' or is_ipv4(ip_address):
                config['ip_address'] = ip_address
            else:
                errors = True
                logging.warning(f'ip_address {ip_address} not valid', 'main:api_config_callback')
        netmask = args.get('netmask')
        if netmask is not None:
            if netmask == '' or (is_ipv4(netmask) and netmask != '0.0.0.0'):
                config['netmask'] = netmask
            else:
                errors = True
                logging.warning(f'netmask {netmask} not valid', 'main:api_config_callback')
        gateway = args.get('gateway')
        if gateway is not None:
            if gateway == '' or is_ipv4(gateway):
                config['gateway'] = gateway
            else:
                errors = True
                logging.warning(f'gateway {gateway} not valid', 'main:api_config_callback')
        dns_server = args.get('dns_server')
        if dns_server is not None:
            if dns_server == '' or is_ipv4(dns_server):
                config['dns_server'] = dns_server
            else:
                errors = True
                logging.warning(f'dns_server {dns_server} not valid', 'main:api_config_callback')
        antenna_bands = args.get('antenna_bands')
        if antenna_bands is not None:
            # bits 0-12 only; anything wider overflows the signed-16 pack and kills every broadcast.
            if len(antenna_bands) == 8 and all(isinstance(b, int) and 0 <= b <= 0x1FFF for b in antenna_bands):
                config['antenna_bands'] = antenna_bands
            else:
                errors = True
                logging.warning(f'antenna_bands {antenna_bands} not valid', 'main:api_config_callback')
        antenna_names = args.get('antenna_names')
        if antenna_names is not None:
            if len(antenna_names) == 8 and all(isinstance(name, str) for name in antenna_names):
                config['antenna_names'] = antenna_names
            else:
                errors = True
                logging.warning(f'antenna_names {antenna_names} not valid', 'main:api_config_callback')
        radio_names = args.get('radio_names')
        if radio_names is not None:
            if len(radio_names) == 2 and all(isinstance(name, str) for name in radio_names):
                config['radio_names'] = radio_names
            else:
                errors = True
                logging.warning(f'radio_names {radio_names} not valid', 'main:api_config_callback')
        if not errors:
            response = b'ok\r\n'
            http_status = HTTP_STATUS_OK
            bytes_sent = await http.send_simple_response(writer, http_status, http.CT_TEXT_TEXT, response)
        else:
            response = b'parameter out of range\r\n'
            http_status = HTTP_STATUS_BAD_REQUEST
            bytes_sent = await http.send_simple_response(writer, http_status, http.CT_TEXT_TEXT, response)
    else:
        response = b'GET or POST only.'
        http_status = HTTP_STATUS_BAD_REQUEST
        bytes_sent = await http.send_simple_response(writer, http_status, http.CT_TEXT_TEXT, response)
    return bytes_sent, http_status


# noinspection PyUnusedLocal
@http_server.route(b'/api/restart')
async def api_restart_callback(http, verb, args, reader, writer, request_headers=None):
    global keep_running

    if upython:
        keep_running = False
        response = b'ok\r\n'
        http_status = HTTP_STATUS_OK
        bytes_sent = await http.send_simple_response(writer, http_status, http.CT_TEXT_TEXT, response)
    else:
        http_status = HTTP_STATUS_BAD_REQUEST
        response = b'not permitted except on PICO-W'
        bytes_sent = await http.send_simple_response(writer, http_status, http.CT_APP_JSON, response)
    return bytes_sent, http_status


@http_server.route(b'/api/status')
async def api_status_callback(http, verb, args, reader, writer, request_headers=None):  # '/api/status'
    radio = safe_int(args.get('radio', -1))
    status = HTTP_STATUS_OK
    if radio == -1:
        payload = {'radio_1_antenna': antennas_selected[0],  # is int (0->8), could be uint8
                   'radio_2_antenna': antennas_selected[1],  # is int (0->8), could be uint8
                   'radio_names': config['radio_names'],     # 2x16 char limit from UI
                   'antenna_names': config['antenna_names'], # 8x20 char limit from UI
                   'antenna_bands': config['antenna_bands'], # 8x int, could be uint16
                   # 'hostname': config['hostname'],         # 64 char limit from UI
                   }
    elif radio == 1 or radio == 2:
        antenna_index = antennas_selected[radio-1]
        if antenna_index <= 0 or antenna_index > 8:
            antenna_name = 'No Antenna'
            antenna_band = 0
        else:
            antenna_name = config['antenna_names'][antenna_index-1]
            antenna_band = config['antenna_bands'][antenna_index-1]
        payload = {'antenna_index': antenna_index,
                   'antenna_name': antenna_name,
                   'antenna_bands':antenna_band,
                   'radio_name': config['radio_names'][radio-1],
                   'radio_number': radio,
                   }
    else:
        payload = {'error': f'invalid radio {radio}'}
        status = HTTP_STATUS_BAD_REQUEST

    bytes_sent = await http.send_simple_response(writer, status, http.CT_APP_JSON, payload)
    return bytes_sent, status


async def select_antenna(radio:int, antenna_requested:int) -> bool:
    global antennas_selected, _select_antenna_lock
    if 1 <= radio <= 2 and 0 <= antenna_requested <= 8:

        async with _select_antenna_lock:
            other_radio = 2 if radio == 1 else 1
            if antenna_requested != 0 and antenna_requested == antennas_selected[other_radio - 1]:
                return False

            antennas_selected[radio - 1] = antenna_requested
            if logging.should_log(logging.DEBUG):
                logging.debug(f'calling set_port({radio}, {antenna_requested})')
            set_port(radio, antenna_requested)
            return True

    return False


@http_server.route(b'/api/select_antenna')
async def api_select_antenna_callback(http, verb, args, reader, writer, request_headers=None):
    radio = safe_int(args.get('radio', '0'))
    antenna_requested = safe_int(args.get('antenna', '0'))
    if 1 <= radio <= 2 and 0 <= antenna_requested <= 8:
        if await select_antenna(radio, antenna_requested):
            http_status = HTTP_STATUS_OK
            payload = {'radio': radio, 'antenna': antenna_requested}
            bytes_sent = await http.send_simple_response(writer, http_status, http.CT_APP_JSON, payload)
            return bytes_sent, http_status  # OUCH! return not at end of func. gnarly.
        else:
            http_status = HTTP_STATUS_CONFLICT
            response = b'Antenna In Use\r\n'
    else:
        response = b'Bad parameter\r\n'
        http_status = HTTP_STATUS_BAD_REQUEST
    bytes_sent = await http.send_simple_response(writer, http_status, http.CT_TEXT_TEXT, response)
    return bytes_sent, http_status


async def serve_serial_client(reader:asyncio.StreamReader, writer:asyncio.StreamWriter):
    """
    send the data over a dumb connection
    """
    t0 = milliseconds()
    partner = writer.get_extra_info('peername')[0]
    logging.info(f'client connected from {partner}', 'main:serve_serial_client')
    client_connected = True

    try:
        while client_connected:
            try:
                data = await asyncio.wait_for(reader.read(1), 60)  # drop silent peers so a stuck client can't hold the socket forever
            except TimeoutError:
                logging.warning('serial client timed out, closing', 'main:serve_serial_client')
                break
            if not data:  # b'' on EOF (peer closed); read() never returns None
                break
            else:
                b = data[0]
                if b == 10:  # line feed, get status
                    payload = {'radio_1_port': antennas_selected[0], 'radio_2_port': antennas_selected[1]}
                    response = json.dumps(payload).encode() + b'\n'
                    writer.write(response)
                elif b == 4 or b == 26 or b == 81 or b == 113:  # ^D/^z/q/Q exit
                    client_connected = False
                await writer.drain()

    except Exception as ex:
        logging.error(f'exception in serve_serial_client: {type(ex)}, {ex}', 'main:serve_serial_client')
    finally:
        try:
            writer.close()
            await writer.wait_closed()
        except Exception as ex:
            logging.warning(f'error closing writer: {ex}', 'main:serve_serial_client')

    tc = milliseconds()
    logging.info(f'client disconnected, elapsed time {(tc - t0) / 1000.0:6.3f} seconds', 'main:serve_serial_client')
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

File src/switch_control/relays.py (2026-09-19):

#
# relays support for AntennaSwitchControl.
#

__author__ = 'J. B. Otterson'
__copyright__ = """
Copyright 2024, 2025, 2026, J. B. Otterson N1KDO.
Redistribution and use in source and binary forms, with or without modification, 
are permitted provided that the following conditions are met:
  1. Redistributions of source code must retain the above copyright notice, 
     this list of conditions and the following disclaimer.
  2. Redistributions in binary form must reproduce the above copyright notice, 
     this list of conditions and the following disclaimer in the documentation 
     and/or other materials provided with the distribution.
THIS SOFTWARE IS PROVIDED BY THE COPYRIGHT HOLDERS AND CONTRIBUTORS "AS IS" AND 
ANY EXPRESS OR IMPLIED WARRANTIES, INCLUDING, BUT NOT LIMITED TO, THE IMPLIED
WARRANTIES OF MERCHANTABILITY AND FITNESS FOR A PARTICULAR PURPOSE ARE DISCLAIMED.
IN NO EVENT SHALL THE COPYRIGHT HOLDER OR CONTRIBUTORS BE LIABLE FOR ANY DIRECT,
INDIRECT, INCIDENTAL, SPECIAL, EXEMPLARY, OR CONSEQUENTIAL DAMAGES (INCLUDING,
BUT NOT LIMITED TO, PROCUREMENT OF SUBSTITUTE GOODS OR SERVICES; LOSS OF USE, 
DATA, OR PROFITS; OR BUSINESS INTERRUPTION) HOWEVER CAUSED AND ON ANY THEORY OF
LIABILITY, WHETHER IN CONTRACT, STRICT LIABILITY, OR TORT (INCLUDING NEGLIGENCE 
OR OTHERWISE) ARISING IN ANY WAY OUT OF THE USE OF THIS SOFTWARE, EVEN IF ADVISED
OF THE POSSIBILITY OF SUCH DAMAGE.
"""
__version__ = '0.2.1'  # 2026-09-18

from utils import upython
import micro_logging as logging

if not upython:
    from not_machine import machine
else:
    import machine

NUM_RELAYS = 8

a_pins = [
    machine.Pin(15, machine.Pin.OUT, value=0),  # A1 GP15 pin 20
    machine.Pin(14, machine.Pin.OUT, value=0),  # A2 GP14 pin 19
    machine.Pin(13, machine.Pin.OUT, value=0),  # A3 GP13 pin 17
    machine.Pin(12, machine.Pin.OUT, value=0),  # A4 GP12 pin 16
    machine.Pin(11, machine.Pin.OUT, value=0),  # A5 GP11 pin 15
    machine.Pin(10, machine.Pin.OUT, value=0),  # A6 GP10 pin 14
    machine.Pin(9, machine.Pin.OUT, value=0),  # A7 GP9 pin 12
    machine.Pin(8, machine.Pin.OUT, value=0),  # A8 GP8 pin 11
]

# define pins for antenna switch port b
b_pins = [
    machine.Pin(7, machine.Pin.OUT, value=0),  # B1 GP7 pin 10
    machine.Pin(6, machine.Pin.OUT, value=0),  # B2 GP6 pin 9
    machine.Pin(5, machine.Pin.OUT, value=0),  # B3 GP5 pin 7
    machine.Pin(4, machine.Pin.OUT, value=0),  # B4 GP4 pin 6
    machine.Pin(3, machine.Pin.OUT, value=0),  # B5 GP3 pin 5
    machine.Pin(2, machine.Pin.OUT, value=0),  # B6 GP2 pin 4
    machine.Pin(1, machine.Pin.OUT, value=0),  # B7 GP1 pin 2
    machine.Pin(0, machine.Pin.OUT, value=0),  # B8 GP0 pin 1
]


def set_port(radio: int, port_selected: int):
    if 0 <= port_selected <= NUM_RELAYS:
        pins = None
        if radio == 1:
            pins = a_pins
        elif radio == 2:
            pins = b_pins
        else:
            logging.error(f'Invalid radio number: {radio}', 'relays:set_port')
            return
        if pins is not None:
            for i in range(len(pins)):
                pins[i].off()
            if port_selected > 0:
                pins[port_selected - 1].on()
    else:
        logging.error(f'Invalid port_selected {port_selected}', 'relays:set_port')

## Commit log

2024-08-18 selected antennas was not properly non-volatile
2024-09-28 add antenna_bands array to status message.
2024-09-29 band change faiiure response message changed
    updated to latest morse code and pico network
2024-09-29 allow 20 chars for antenna names
2024-10-30 add BOM, clean up schematic
    [AntennaSwitchControl.kicad_pcb, AntennaSwitchControl.kicad_sch]
2024-10-31 added molex pins for connectors
2024-12-14 add support for NO antenna selected
    tolerate some connection failures better
    use constants for http response codes
    [main.py, relays.py]
2024-12-31 fix default config item names
    [main.py]
2025-01-05 add pricing to BOM
2025-02-01 v 2.0 hardware.
    swap out connectors
    move connectors to back of board
    reallocate port outputs
    move pico-w to edge of board.
    [AntennaSwitchControl.kicad_pcb, AntennaSwitchControl.kicad_sch]
2025-03-13 fix off by one error.
    [relays.py]
2025-03-16 add new board image
2025-03-18 fix off-by-one.
    still ugly
    [main.py]
2025-03-24 # Conflicts: # src/switch_control/http_server.py
    [AntennaSwitchControl.kicad_pcb, AntennaSwitchControl.kicad_sch]
2025-05-02 fix up debug logging
    [uping.py]
2025-05-03 log configuration post api failures
    [main.py]
2025-09-19 sent udp broadcasts of switch status
2025-12-29 fix edge case, improve logging
    [relays.py]
2025-12-31 update date on relays.py
2025-12-31 add new --bootloader option
    this is for when you cannot access the
    little white button, perhaps because the
    module is in an enclosure
2026-01-07 try to improve layout on mobile devices
2026-01-07 improve layout on mobile devices
2026-05-20 latest ntp.py has better error logging
    [ntp.py]
2026-05-20 fix broadcast to use current config values. improve logging to enable debugging
2026-06-11 fix error payload typo.
    [main.py]

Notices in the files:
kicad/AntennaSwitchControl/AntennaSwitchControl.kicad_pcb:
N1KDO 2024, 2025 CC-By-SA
